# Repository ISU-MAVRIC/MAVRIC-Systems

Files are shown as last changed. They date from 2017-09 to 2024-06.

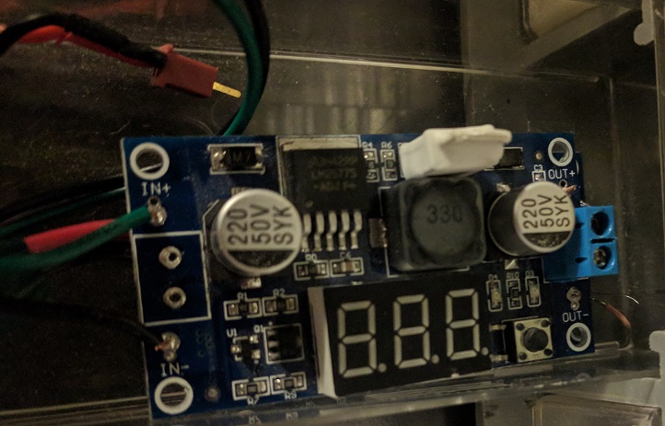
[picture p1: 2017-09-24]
Electrical/Images of Components/Step-Up.jpg

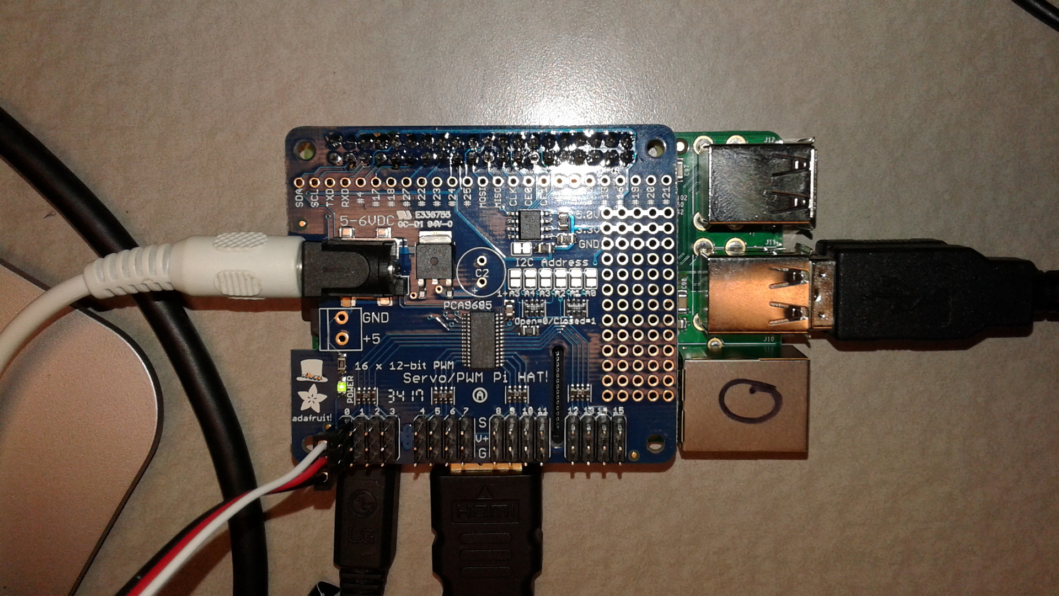
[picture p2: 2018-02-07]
Electrical/Images of Components/Pi-PWM-hat.jpg

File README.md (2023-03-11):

# MAVRIC-Systems
The repository for the Systems Team. Contains all resources pertaining to the Systems Team, including: rover and base station code, custom PCB designs, electrical diagrams, and rover documentation. Clone this repository to your computer with Git Bash, GitHub Desktop, or another Git client to edit files. Talk to the current Systems Team Lead or the current MAVRIC Project Manager to get commit access so you can push your changes to the repository.

## Repository Structure
MAVRIC maintains two rovers as of 12/2020: the previous-generation Phoenix and the next-gen Scarab. The code for Phoenix was captured as a GitHub release and can be viewed by checking out the _Phoenix - Stable_ release, tagged `v1.0.0`. Use `git checkout v1.0.0` in Git Bash or the equivalent feature in your Git client to load the Phoenix code. Each rover's code will be tagged with a release name and version number once it is complete; this repository will otherwise reflect the code state of the most recent rover in development.

Newer code is not backwards-compatible with previous generation rovers. For example, the base station software intended for use with Scarab is not compatible with Phoenix.

## Wiki Documentation
Documentation about MAVRIC rovers, past and present, is recorded using the GitHub Wiki feature. Click the _Wiki_ tab on the MAVRIC-Systems web page to open the wiki, then use the links in the sidebar to navigate to various wiki pages. Most information is up to date and the difference should be very noticeable, but if you are not able to tell the difference between current and outdated information, ask the current Systems Team Lead about it. Remember that this repository contains documentation for multiple rovers, so information that appears outdated may simply document a different rover than the one currently being developed.

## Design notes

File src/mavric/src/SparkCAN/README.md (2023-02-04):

# MAVRIC SparkMax ESC Library

A library for controlling SparkMax Electronic Speed Controllers using python and a CAN Bus.

## IMPORTANT NOTE
*Motor controllers must have ramping enabled if running at more than 50% power, otherwise the motor will try to instantly go to the power level and will stutter.*

## Dependancies

- Python 3 (Not tested on 2.7)
- python-can (https://python-can.readthedocs.io/en/master/)

# Example Control and Encoder Feedback Code

```python
from SparkCAN import SparkBus
import time

#Instantiate SparkBus object
bus = SparkBus(channel="can0", bustype='socketcan', bitrate=1000000)
#Create a new controller with CAN id 1
sparkESC = bus.init_controller(1)
time.sleep(1)
#Set motor to 50% power
sparkESC.percent_output(.5) #50%
#Prints the velocity 10 times, you should be able to see it ramp up as the motor gets up to speed.
for i in range(10):
    print(sparkESC.velocity)
    time.sleep(0.001)
#wait 5 seconds
time.sleep(5)
#Set motor to 0% power
sparkESC.percent_output(0)
```

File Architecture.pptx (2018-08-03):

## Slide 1

Wheel Driver

Wheel Driver

Arm

Legend:
Power
Signal
Module

Power Relays should Have a local override

Arm Control Board

Power Relay

Wheel Driver

Drive Control Board

Master Control Board

Wheel Driver

Power Relay

Power Relay

Communications
(radios)

Master Switch

Battery

Battery

Wheel Driver

Wheel Driver

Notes: Electrical architecture. Shows power systems, components, and communication lines.

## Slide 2

Legend:
Power
Signal
Module

Drive Control Board

Arm

Wheel Driver

Arm Control Board

Wheel Driver

Master Control Board

Wheel Driver

Wheel Driver

Communications
(radios)

Master Switch

Wheel Driver

Battery

Wheel Driver

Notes: Electrical architecture. Shows power systems, components, and communication lines.

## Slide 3

Drive Control Board

Speed Control

Wheel Control

Left

Right

External Debug
(Sees everything, renders whatever we need to the user)
(May comprise of rqt tools)

Soil Science System

Controller
Collection
Sensors

Arm Control Board

- Linear Actuator Driver
- DC Motor Driver

Servo Driver
(smoothing etc.
included)

Right

Left

Commands

ROS Interface

Inverse Kinematics (opt)

ROS Interface

Master Control Board

ROS Interface

ROS Interface

GPS

Base Station Interface

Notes: ROS Architecture. Structure of nodes (lines are topics).

The Comms. Interface nodes will handle communication between the boards. They are intended as the only interface between boards. To be clear: the master control board should not publish or subscribe to internal topics of the other boards.

The base station may communicate over ROS, but that will depend on the network reliability, and on if we are using a TCP/IP enabled communications system.

The Inverse Kinematics node may or may not exist in reality. It will certainty not exist in rev1.

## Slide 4

Motor Driver

Arm Control Board

Master Control Board

Legend:
Power
Signal
Module

5V Reg.

Communications
(network)

Power Source

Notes: Electrical architecture. Shows power systems, components, and communication lines.

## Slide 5

Arm Control Board

Master Control Board

Translation to ROS

Network Port

Analog in

Control System (closed loop)

PWM out

Subscriber

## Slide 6

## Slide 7

/

Drive Board HW/

PCA9685 PWM HAT/
Driver module for the HAT, takes in wither duty cycle or pulse time inputs.
Frequency is set by a parameter (startup)

Arm Board HW/

PCA9685 PWM HAT
Driver module for the HAT, takes in wither duty cycle or pulse time inputs.
Frequency is set by a parameter (startup)

Switch Inputs (PiGPIO)
Reads a GPIO pin and publishes out the results
Frequency is set by a parameter (startup)

Master Board HW/

PCA9685 PWM HAT
Driver module for the HAT, takes in wither duty cycle or pulse time inputs.
Frequency is set by a parameter (startup)

GPS Module (serial)
Retrieves and publishes the current GPS data

Arm/

Actuator Interface
Receives commands for an actuator and publishes them.

Actuator Limiting
Limits the value of an actuator command when configured switches are active.

Mapping
Scales the outputs for the PWM board

Drive/

Drivetrain Interface
Receives commands and publishes them in pairs (left, right)

Drivetrain Hartbeat
Monitors for a gap in the drivetrain command pairs and stops the rover

Drivetrain Control
Subscribes to drive command pairs and outputs the individual motor values

Mapping
Scales the motor outputs for the PWM outputs.

System Cooling/

PID Controller
Monitors temperature and outputs speed to the fans (via PWM controller)

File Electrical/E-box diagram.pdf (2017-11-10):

Room for wires for front two Pis

Main Control | Drive
Science | Arm control

Room for wires for front two Pis

IO port and room for connectors | IO port and room for connectors
H‐Bridge | H‐Bridge

Reserved For Sensors
(Like GPS)

Switch Board of unknown size

Regulator | Regulator
Regulator | Regulator

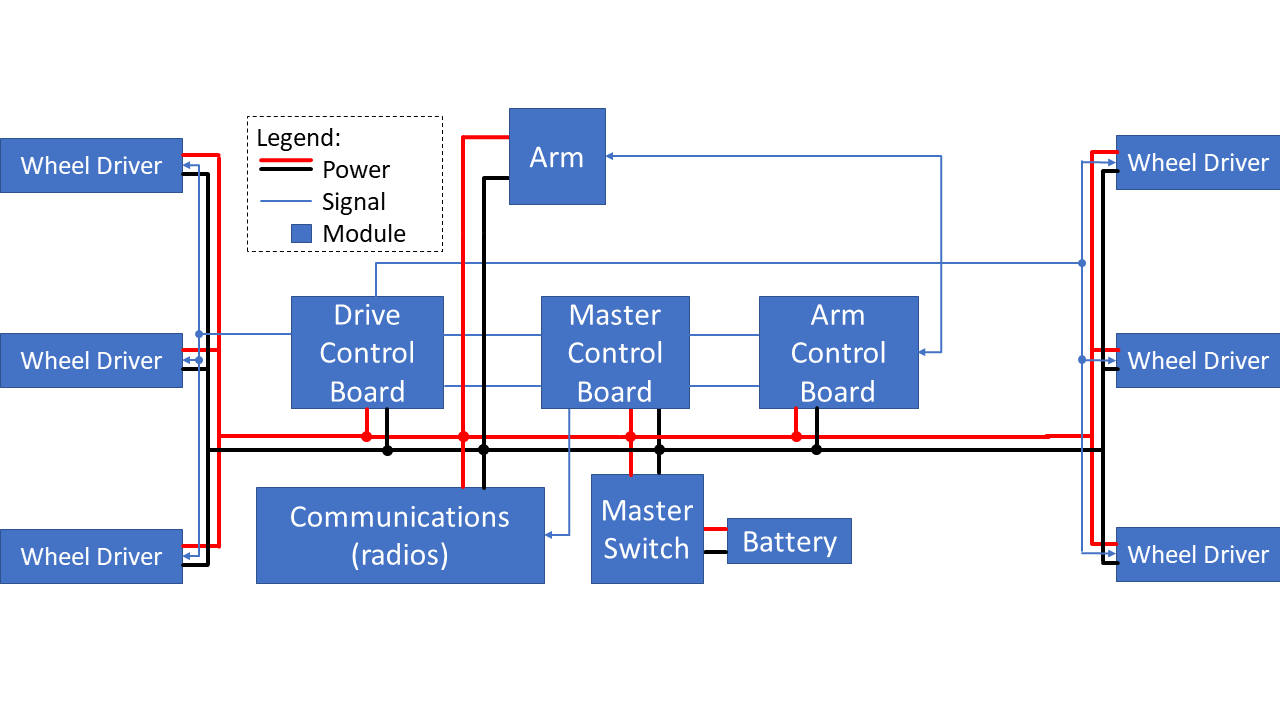
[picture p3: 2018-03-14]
Electrical/ElectricalArchitecture.png

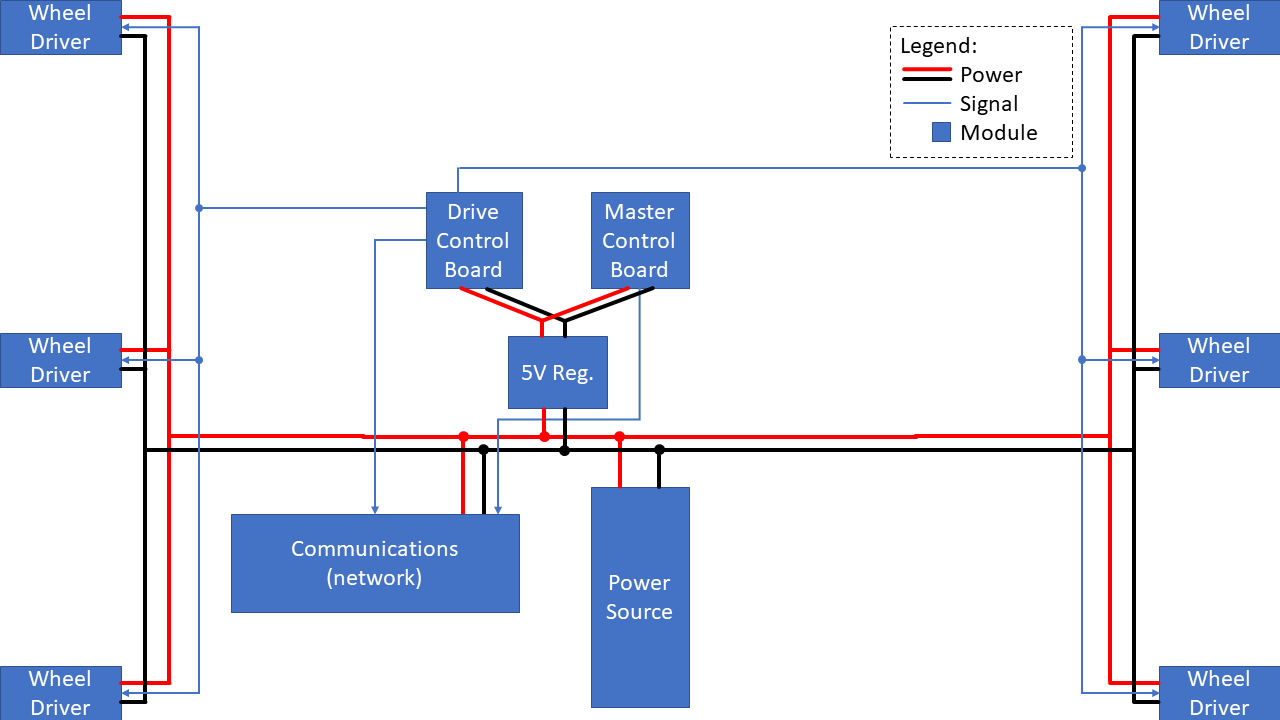
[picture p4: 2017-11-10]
Electrical/Milestone1 Electrical.PNG

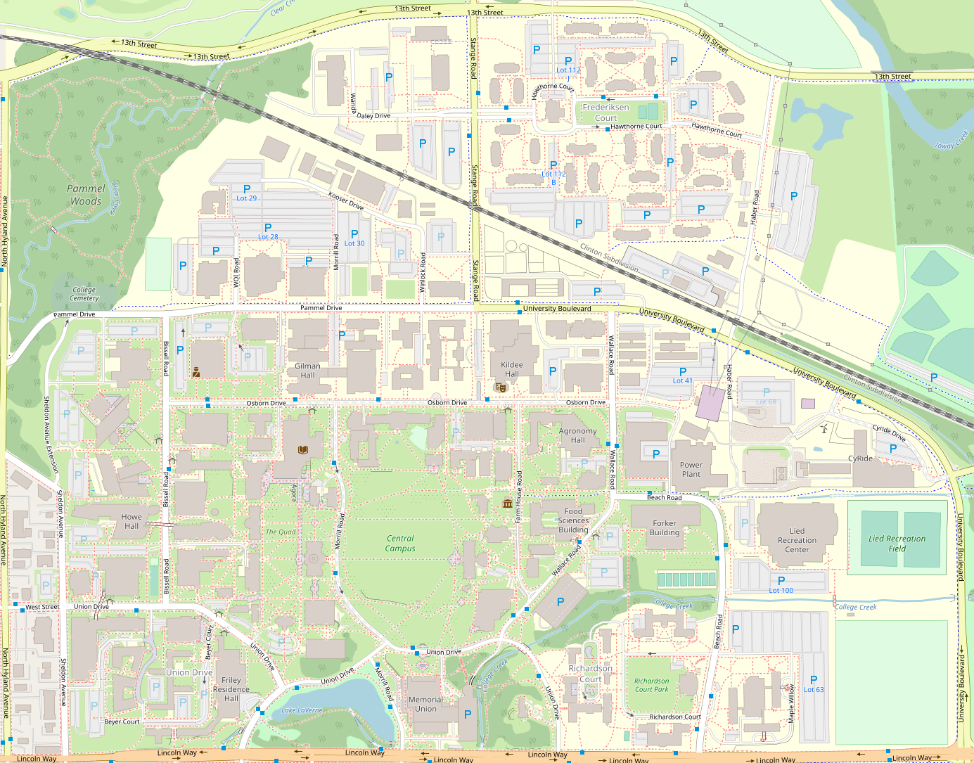
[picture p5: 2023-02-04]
Base Station/Scarab Base Station/maps/map.png

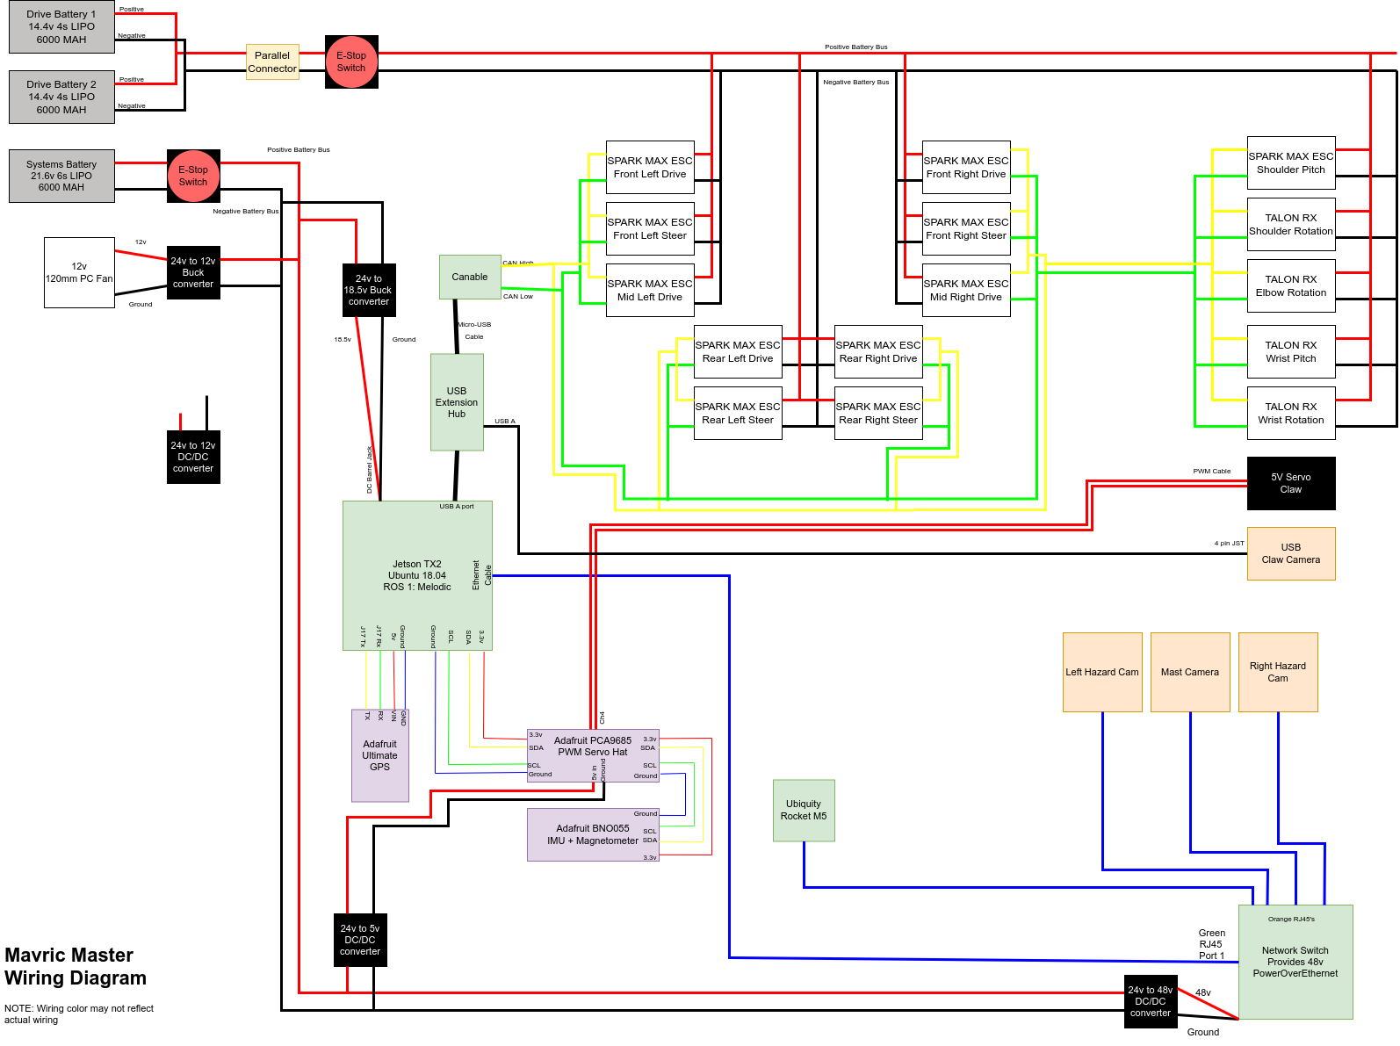
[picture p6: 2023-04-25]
Electrical/MasterDiagram.drawio.png

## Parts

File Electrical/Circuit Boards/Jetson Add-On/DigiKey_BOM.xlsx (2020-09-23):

Qty | Part number | Description | Total
2 | 568-8366-5-ND | PWM Driver IC | $4.52
2 | 296-49939-1-ND | CAN Transceiver IC | $5.36
1 | LTC2309CF#PBF-ND | ADC IC | $7.34
1 | PPPC152LFBN-RC | 30-Pin Header | $1.89
1 | 36-3000-ND | Coin Cell Holder | $0.54
1 | https://www.adafruit.com/product/2223 | GPIO Stacking Header | $2.50
1 | https://www.adafruit.com/product/790 | GPS Module | $29.95
 |  | Grand Total | $19.65

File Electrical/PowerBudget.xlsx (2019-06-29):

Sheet: Component Data
ID | Name | Manufacturer | Source | Notes | Price | Peak Consumption (W) | Constant Consumption (W) | Output (V) | Output Current Limit (A) | Discharge (for batteries) | Battery (mAh) | Thoughput Loss
LiFePo |  |  |  |  |  | 0.0 | 0.0 | 28.8 |  | 10C | 10000.0 | 0.00%
Large LiPo | 22.2 V Lithuim Polymer Battery back | BatterySpace | http://www.batteryspace.com/lipo-battery-pack-tattu-22-2v-12ah-266wh-15c-6s1p.aspx |  | $254.00 | 0.0 | 0.0 | 22.2 |  | 15C | 12000.0 | 0.00%
Small LiPo | 22.2 V Lithuim Polymer Battery back |  |  |  |  | 0.0 | 0.0 | 22.2 |  | 15C | 5200.0 | 0.00%
LiIon | 22.2V Lithium Ion Battery Pack |  |  | Obtained from Lab leftovers | $0.00 |  |  | 21.6 |  | 5C | 7800.0 | 0.00%
Regulator | Adjustable Linear Voltage Regulator | Aihasd | https://www.aliexpress.com/item/DC-Adjustable-Voltage-Regulator-Module-DC-4-5-30V-to-0-8-30V-12A-Buck-Converters/1724570414.html |  | $8.48 | 0.0 | 0.0 |  | 12.0 |  |  | 10.00%
Raspberry Pi | Raspberry Pi 3 Rev 1.2 |  |  |  | $30.00 | 7.0 | 4.0 | 3.3 | 0.5 |  |  | 0.00%
RM5 | Ubiquity Rocket M5 | Ubiquity | http://www.doubleradius.com/s.nl/sc.1/category./.f?search=rocket+m3 |  | $180.00 | 8.0 | 6.0 |  |  |  |  | 0.00%
Victor SP | Victor SP DC Motor Driver | Cross The Road Electronics | https://www.vexrobotics.com/217-9090.html |  | $60.00 | 0.0 | 0.0 | 12.0 | 60.0 |  |  | 10.00%
Talon SRX | Talon SRX DC Motor Driver | Cross The Road Electronics |  |  | $90.00 | 0.0 | 0.0 | [INPUT] | 60.0 |  |  | 10.00%
Wheel Motor | Banebots RS-550 Motor 19300rpm 12V 70.55oz-in | BaneBot | http://robotshop.com/en/banebots-rs-550-motor-12v-19300rpm.html |  | $7.25 | 222.0 | 37.0 |  |  |  |  | 0.00%
20A 24V->12V Regulator | Nextrox DC/DC Converter Regulator 24V Step Down to 12V 20A 240W |  | https://www.amazon.com/Nextrox-Converter-Regulator-Step-Down/dp/B00BWKXTUU | 12-40V input | $16.00 | 0.0 | 0.0 | 12.0 | 20.0 |  |  | 10.00%
Network Switch | 16-Port network switch |  |  |  | $60.00 | 24.0 | 8.0 |  |  |  |  | 0.00%
Power Rail | Virtual Node for system isolation |  |  |  | $0.00 | 0.0 | 0.0 | [INPUT] |  |  |  | 0.00%
PC Fan | ??? |  |  | 12V 4-pin PC Fan | $18.00 | 12.0 | 6.3 |  |  |  |  | 0.00%
IP Camera | ELP 1280720p 1MP Camera |  | https://www.amazon.com/ELP-1280720p-Megapixel-Camera-Network/dp/B00KA4M4WS |  | $20.00 | 12.0 | 6.0 |  |  |  |  | 0.00%
Arm Shoulder |  |  |  |  |  | 200.0 | 24.0 |  |  |  |  | 0.00%
Arm Elbow |  |  |  |  |  | 10.0 | 1.0 |  |  |  |  | 0.00%
Arm Wrist |  |  |  |  |  | 10.0 | 2.0 |  |  |  |  | 0.00%
Jetson TX2 |  |  |  |  |  | 70.0 | 50.0 |  |  |  |  | 0.00%

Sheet: Items
ItemID | Component | Supply Item | Supply Component | Name | Manufacturer | Source | Price | Peak Consumption (W) | Constant Consumption (W) | Output (V) | Output (A) | Battery (mAh) | Thoughput Loss
Primary Battery Pack | Large LiPo |  |  | 22.2 V Lithuim Polymer Battery back | BatterySpace | http://www.batteryspace.com/lipo-battery-pack-tattu-22-2v-12ah-266wh-15c-6s1p.aspx | $254.00 | 0.0 | 0.0 | 22.2 | 180.0 | 12000.0 | 0.00%
E-Box Battery | Small LiPo |  |  | 22.2 V Lithuim Polymer Battery back |  |  |  | 0.0 | 0.0 | 22.2 | 78.0 | 5200.0 | 0.00
Logic Supply | Regulator | E-Box Battery | Small LiPo | Adjustable Linear Voltage Regulator | Aihasd | https://www.aliexpress.com/item/DC-Adjustable-Voltage-Regulator-Module-DC-4-5-30V-to-0-8-30V-12A-Buck-Converters/1724570414.html | $8.48 | 0.0 | 0.0 | 19.5 | 5.1 |  | 10.00%
Network Power | Regulator | E-Box Battery | Small LiPo | Adjustable Linear Voltage Regulator | Aihasd | https://www.aliexpress.com/item/DC-Adjustable-Voltage-Regulator-Module-DC-4-5-30V-to-0-8-30V-12A-Buck-Converters/1724570414.html | $8.48 | 0.0 | 0.0 | 12.0 | 12.0 |  | 10.00%
Transceiver | RM5 | Network Power | Regulator | Ubiquity Rocket M5 | Ubiquity | http://www.doubleradius.com/s.nl/sc.1/category./.f?search=rocket+m3 | $180.00 | 8.0 | 6.0 |  | 0.0 |  | 0.00%
Network Switch | Network Switch | Network Power | Regulator | 16-Port network switch |  |  | $60.00 | 24.0 | 8.0 |  | 0.0 |  | 0.00%
Arm Power | 20A 24V->12V Regulator | Primary Battery Pack | Large LiPo | Nextrox DC/DC Converter Regulator 24V Step Down to 12V 20A 240W |  | https://www.amazon.com/Nextrox-Converter-Regulator-Step-Down/dp/B00BWKXTUU | $16.00 | 0.0 | 0.0 | 12.0 | 20.0 |  | 10.00%
Drivetrain Power | Power Rail | Primary Battery Pack | Large LiPo | Virtual Node for system isolation |  |  | $0.00 | 0.0 | 0.0 | 22.2 | 400.0 |  | 0.00%
FrontRight ESC | Talon SRX | Drivetrain Power | Power Rail | Talon SRX DC Motor Driver | Cross The Road Electronics |  | $90.00 | 0.0 | 0.0 | 22.2 | 60.0 |  | 10.00%
FrontRight Motor | Wheel Motor | FrontRight ESC | Talon SRX | Banebots RS-550 Motor 19300rpm 12V 70.55oz-in | BaneBot | http://robotshop.com/en/banebots-rs-550-motor-12v-19300rpm.html | $7.25 | 222.0 | 37.0 |  | 0.0 |  | 0.00%
MidRight ESC | Talon SRX | Drivetrain Power | Power Rail | Talon SRX DC Motor Driver | Cross The Road Electronics |  | $90.00 | 0.0 | 0.0 | 22.2 | 60.0 |  | 10.00%
MidRight Motor | Wheel Motor | MidRight ESC | Talon SRX | Banebots RS-550 Motor 19300rpm 12V 70.55oz-in | BaneBot | http://robotshop.com/en/banebots-rs-550-motor-12v-19300rpm.html | $7.25 | 222.0 | 37.0 |  | 0.0 |  | 0.00%
BackRight ESC | Talon SRX | Drivetrain Power | Power Rail | Talon SRX DC Motor Driver | Cross The Road Electronics |  | $90.00 | 0.0 | 0.0 | 22.2 | 60.0 |  | 10.00%
BackRight Motor | Wheel Motor | BackRight ESC | Talon SRX | Banebots RS-550 Motor 19300rpm 12V 70.55oz-in | BaneBot | http://robotshop.com/en/banebots-rs-550-motor-12v-19300rpm.html | $7.25 | 222.0 | 37.0 |  | 0.0 |  | 0.00%
FrontLeft ESC | Talon SRX | Drivetrain Power | Power Rail | Talon SRX DC Motor Driver | Cross The Road Electronics |  | $90.00 | 0.0 | 0.0 | 22.2 | 60.0 |  | 10.00%
FrontLeft Motor | Wheel Motor | FrontLeft ESC | Talon SRX | Banebots RS-550 Motor 19300rpm 12V 70.55oz-in | BaneBot | http://robotshop.com/en/banebots-rs-550-motor-12v-19300rpm.html | $7.25 | 222.0 | 37.0 |  | 0.0 |  | 0.00%
MidLeft ESC | Talon SRX | Drivetrain Power | Power Rail | Talon SRX DC Motor Driver | Cross The Road Electronics |  | $90.00 | 0.0 | 0.0 | 22.2 | 60.0 |  | 10.00%
MidLeft Motor | Wheel Motor | MidLeft ESC | Talon SRX | Banebots RS-550 Motor 19300rpm 12V 70.55oz-in | BaneBot | http://robotshop.com/en/banebots-rs-550-motor-12v-19300rpm.html | $7.25 | 222.0 | 37.0 |  | 0.0 |  | 0.00%
BackLeft ESC | Talon SRX | Drivetrain Power | Power Rail | Talon SRX DC Motor Driver | Cross The Road Electronics |  | $90.00 | 0.0 | 0.0 | 22.2 | 60.0 |  | 10.00%
BackLeft Motor | Wheel Motor | BackLeft ESC | Talon SRX | Banebots RS-550 Motor 19300rpm 12V 70.55oz-in | BaneBot | http://robotshop.com/en/banebots-rs-550-motor-12v-19300rpm.html | $7.25 | 222.0 | 37.0 |  | 0.0 |  | 0.00%
Cooling Fans Power | Regulator | E-Box Battery | Small LiPo | Adjustable Linear Voltage Regulator | Aihasd | https://www.aliexpress.com/item/DC-Adjustable-Voltage-Regulator-Module-DC-4-5-30V-to-0-8-30V-12A-Buck-Converters/1724570414.html | $8.48 | 0.0 | 0.0 | 12.0 | 12.0 |  | 0.10
Colling Fan 1 | PC Fan | Cooling Fans Power | Regulator | ??? |  |  | $18.00 | 12.0 | 6.3 |  | 0.0 |  | 0.00
Colling Fan 2 | PC Fan | Cooling Fans Power | Regulator | ??? |  |  | $18.00 | 12.0 | 6.3 |  | 0.0 |  | 0.00
Colling Fan 3 | PC Fan | Cooling Fans Power | Regulator | ??? |  |  | $18.00 | 12.0 | 6.3 |  | 0.0 |  | 0.00
Colling Fan 4 | PC Fan | Cooling Fans Power | Regulator | ??? |  |  | $18.00 | 12.0 | 6.3 |  | 0.0 |  | 0.00
 |  | Cooling Fans Power | Regulator
 |  | Cooling Fans Power | Regulator
 |  | Cooling Fans Power | Regulator
 |  | Cooling Fans Power | Regulator
Hazard Camera 1 | IP Camera | Network Power | Regulator | ELP 1280720p 1MP Camera |  | https://www.amazon.com/ELP-1280720p-Megapixel-Camera-Network/dp/B00KA4M4WS | $20.00 | 12.0 | 6.0 |  | 0.0 |  | 0.00
Hazard Camera 2 | IP Camera | Network Power | Regulator | ELP 1280720p 1MP Camera |  | https://www.amazon.com/ELP-1280720p-Megapixel-Camera-Network/dp/B00KA4M4WS | $20.00 | 12.0 | 6.0 |  | 0.0 |  | 0.00
Hazard Camera 3 | IP Camera | Network Power | Regulator | ELP 1280720p 1MP Camera |  | https://www.amazon.com/ELP-1280720p-Megapixel-Camera-Network/dp/B00KA4M4WS | $20.00 | 12.0 | 6.0 |  | 0.0 |  | 0.00
Arm Shoulder | Arm Shoulder | Arm Power | 20A 24V->12V Regulator |  |  |  |  | 200.0 | 24.0 |  | 0.0 |  | 0.00
Arm Elbow | Arm Elbow | Arm Power | 20A 24V->12V Regulator |  |  |  |  | 10.0 | 1.0 |  | 0.0 |  | 0.00
Arm Wrist1 | Arm Wrist | Arm Power | 20A 24V->12V Regulator |  |  |  |  | 10.0 | 2.0 |  | 0.0 |  | 0.00
Arm Wrist2 | Arm Wrist | Arm Power | 20A 24V->12V Regulator |  |  |  |  | 10.0 | 2.0 |  | 0.0 |  | 0.00
Control Board | Jetson TX2 | Logic Supply | Regulator |  |  |  |  | 70.0 | 50.0 |  | 0.0 |  | 0.00

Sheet: Analysis
ItemID | Supply Item | Input (V) | Output (V) | Peak Output (A) | Constant Output (A) | Peak Input (A) | Constant Input (A) | Thoughput Loss | Self Peak Consumption (W) | Children Peak Consumption (W) | Total Peak Consumption (W) | Self Constant Consumption (W) | Children Constant Consumption (W) | Total Constant Consumption (W)
Primary Battery Pack |  |  | 22.2 | 77.4 | 12.4 |  |  | 0.00 | 0.0 | 1718.2 | 1718.2 | 0.0 | 276.1 | 276.1
E-Box Battery |  |  | 22.2 | 9.2 | 5.3 |  |  | 0.00 | 0.0 | 204.6 | 204.6 | 0.0 | 117.9 | 117.9
Logic Supply | E-Box Battery | 22.2 | 19.5 | 3.6 | 2.6 | 3.5 | 2.5 | 0.10 | 7.0 | 70.0 | 77.0 | 5.0 | 50.0 | 55.0
Network Power | E-Box Battery | 22.2 | 12 | 5.7 | 2.7 | 3.4 | 1.6 | 0.10 | 6.8 | 68.0 | 74.8 | 3.2 | 32.0 | 35.2
Transceiver | Network Power | 12 |  |  |  | 0.7 | 0.5 | 0.00 | 8.0 | 0.0 | 8.0 | 6.0 | 0.0 | 6.0
Network Switch | Network Power | 12 |  |  |  | 2.0 | 0.7 | 0.00 | 24.0 | 0.0 | 24.0 | 8.0 | 0.0 | 8.0
Arm Power | Primary Battery Pack | 22.2 | 12 | 19.2 | 2.4 | 11.4 | 1.4 | 0.10 | 23.0 | 230.0 | 253.0 | 2.9 | 29.0 | 31.9
Drivetrain Power | Primary Battery Pack | 22.2 | 22.2 | 66.0 | 11.0 | 66.0 | 11.0 | 0.00 | 0.0 | 1465.2 | 1465.2 | 0.0 | 244.2 | 244.2
FrontRight ESC | Drivetrain Power | 22.2 | 22.2 | 10.0 | 1.7 | 11.0 | 1.8 | 0.10 | 22.2 | 222.0 | 244.2 | 3.7 | 37.0 | 40.7
FrontRight Motor | FrontRight ESC | 22.2 |  |  |  | 10.0 | 1.7 | 0.00 | 222.0 | 0.0 | 222.0 | 37.0 | 0.0 | 37.0
MidRight ESC | Drivetrain Power | 22.2 | 22.2 | 10.0 | 1.7 | 11.0 | 1.8 | 0.10 | 22.2 | 222.0 | 244.2 | 3.7 | 37.0 | 40.7
MidRight Motor | MidRight ESC | 22.2 |  |  |  | 10.0 | 1.7 | 0.00 | 222.0 | 0.0 | 222.0 | 37.0 | 0.0 | 37.0
BackRight ESC | Drivetrain Power | 22.2 | 22.2 | 10.0 | 1.7 | 11.0 | 1.8 | 0.10 | 22.2 | 222.0 | 244.2 | 3.7 | 37.0 | 40.7
BackRight Motor | BackRight ESC | 22.2 |  |  |  | 10.0 | 1.7 | 0.00 | 222.0 | 0.0 | 222.0 | 37.0 | 0.0 | 37.0
FrontLeft ESC | Drivetrain Power | 22.2 | 22.2 | 10.0 | 1.7 | 11.0 | 1.8 | 0.10 | 22.2 | 222.0 | 244.2 | 3.7 | 37.0 | 40.7
FrontLeft Motor | FrontLeft ESC | 22.2 |  |  |  | 10.0 | 1.7 | 0.00 | 222.0 | 0.0 | 222.0 | 37.0 | 0.0 | 37.0
MidLeft ESC | Drivetrain Power | 22.2 | 22.2 | 10.0 | 1.7 | 11.0 | 1.8 | 0.10 | 22.2 | 222.0 | 244.2 | 3.7 | 37.0 | 40.7
MidLeft Motor | MidLeft ESC | 22.2 |  |  |  | 10.0 | 1.7 | 0.00 | 222.0 | 0.0 | 222.0 | 37.0 | 0.0 | 37.0
BackLeft ESC | Drivetrain Power | 22.2 | 22.2 | 10.0 | 1.7 | 11.0 | 1.8 | 0.10 | 22.2 | 222.0 | 244.2 | 3.7 | 37.0 | 40.7
BackLeft Motor | BackLeft ESC | 22.2 |  |  |  | 10.0 | 1.7 | 0.00 | 222.0 | 0.0 | 222.0 | 37.0 | 0.0 | 37.0
Cooling Fans Power | E-Box Battery | 22.2 | 12 | 4.0 | 2.1 | 2.4 | 1.2 | 0.10 | 4.8 | 48.0 | 52.8 | 2.5 | 25.2 | 27.7
Colling Fan 1 | Cooling Fans Power | 12 |  |  |  | 1.0 | 0.5 | 0.00 | 12.0 | 0.0 | 12.0 | 6.3 | 0.0 | 6.3
Colling Fan 2 | Cooling Fans Power | 12 |  |  |  | 1.0 | 0.5 | 0.00 | 12.0 | 0.0 | 12.0 | 6.3 | 0.0 | 6.3
Colling Fan 3 | Cooling Fans Power | 12 |  |  |  | 1.0 | 0.5 | 0.00 | 12.0 | 0.0 | 12.0 | 6.3 | 0.0 | 6.3
Colling Fan 4 | Cooling Fans Power | 12 |  |  |  | 1.0 | 0.5 | 0.00 | 12.0 | 0.0 | 12.0 | 6.3 | 0.0 | 6.3
Hazard Camera 1 | Network Power | 12 |  |  |  | 1.0 | 0.5 | 0.00 | 12.0 | 0.0 | 12.0 | 6.0 | 0.0 | 6.0
Hazard Camera 2 | Network Power | 12 |  |  |  | 1.0 | 0.5 | 0.00 | 12.0 | 0.0 | 12.0 | 6.0 | 0.0 | 6.0
Hazard Camera 3 | Network Power | 12 |  |  |  | 1.0 | 0.5 | 0.00 | 12.0 | 0.0 | 12.0 | 6.0 | 0.0 | 6.0
Arm Shoulder | Arm Power | 12 |  |  |  | 16.7 | 2.0 | 0.00 | 200.0 | 0.0 | 200.0 | 24.0 | 0.0 | 24.0
Arm Elbow | Arm Power | 12 |  |  |  | 0.8 | 0.1 | 0.00 | 10.0 | 0.0 | 10.0 | 1.0 | 0.0 | 1.0
Arm Wrist1 | Arm Power | 12 |  |  |  | 0.8 | 0.2 | 0.00 | 10.0 | 0.0 | 10.0 | 2.0 | 0.0 | 2.0
Arm Wrist2 | Arm Power | 12 |  |  |  | 0.8 | 0.2 | 0.00 | 10.0 | 0.0 | 10.0 | 2.0 | 0.0 | 2.0
Control Board | Logic Supply | 19.5 |  |  |  | 3.6 | 2.6 | 0.00 | 70.0 | 0.0 | 70.0 | 50.0 | 0.0 | 50.0

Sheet: Results
ItemID | Peak % Capacity | Constant % Capacity | Battery Life (hrs) |  |  | Power Rail | Voltage (V) | Current (A) | Peak Current (A) | Power (W)
 |  |  |  |  |  | Primary Battery Pack | 22.20 | 12.44 | 77.40 | 1718.20
Primary Battery Pack | 43.00% | 6.91% | 0.96 | Status: | GO | E-Box Battery | 22.20 | 5.31 | 9.22 | 204.60
E-Box Battery | 11.82% | 6.81% | 0.98 | Battery Life: | 57.9 min
Logic Supply | 70.00% | 50.00%
Network Power | 47.22% | 22.22%
Transceiver
Network Switch
Arm Power | 95.83% | 12.08%
Drivetrain Power | 16.50% | 2.75%
FrontRight ESC | 16.67% | 2.78%
FrontRight Motor
MidRight ESC | 16.67% | 2.78%
MidRight Motor
BackRight ESC | 16.67% | 2.78%
BackRight Motor
FrontLeft ESC | 16.67% | 2.78%
FrontLeft Motor
MidLeft ESC | 16.67% | 2.78%
MidLeft Motor
BackLeft ESC | 16.67% | 2.78%
BackLeft Motor
Cooling Fans Power | 33.33% | 17.50%
Colling Fan 1
Colling Fan 2
Colling Fan 3
Colling Fan 4
Hazard Camera 1
Hazard Camera 2
Hazard Camera 3
Arm Shoulder
Arm Elbow
Arm Wrist1

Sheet: Motor Characterization
Speed (RPM) | Torque (N·m) | Current (A) | Voltage | K_s | K_t | R | Speed (RPM) | Torque (N·m) | Current (A)
0 | 0.358 | 71.235 | 12 | 0.0008409330918 | 198.98 A/Nm | 0.168 Ohm | 2.38788245e-05 | 0.358 | 71.2350262
142.699 | 0.35442 | 70.56 |  |  |  | Equation | 142.70 | 0.35442 | 70.52267594
285.397 | 0.35084 | 69.885 | Stall Current | Stall Torque | No-Load Speed | Vin=(0.00084093309V/RPM)*RPM +(198.98052011798A/Nm)*(0.16845645492Ohm)*(Load Nm) | 285.40 | 0.35084 | 69.81032568
428.096 | 0.34726 | 69.21 | 71.24 A | 0.36 Nm | 14269.86299 RPM |  | 428.10 | 0.34726 | 69.09797542
570.795 | 0.34368 | 68.535 |  |  |  |  | 570.79 | 0.34368 | 68.38562515
713.493 | 0.3401 | 67.861 |  |  |  |  | 713.49 | 0.3401 | 67.67327489
856.192 | 0.33652 | 67.186 |  |  |  |  | 856.19 | 0.33652 | 66.96092463
998.89 | 0.33294 | 66.511 |  |  |  |  | 998.89 | 0.33294 | 66.24857437
1141.589 | 0.32936 | 65.836 |  |  |  |  | 1141.59 | 0.32936 | 65.53622411
1284.288 | 0.32578 | 65.161 |  |  |  |  | 1284.29 | 0.32578 | 64.82387384
1426.986 | 0.3222 | 64.486 |  |  |  |  | 1426.99 | 0.3222 | 64.11152358
1569.685 | 0.31862 | 63.811 |  |  |  |  | 1569.68 | 0.31862 | 63.39917332
1712.384 | 0.31504 | 63.136 |  |  |  |  | 1712.38 | 0.31504 | 62.68682306
1855.082 | 0.31146 | 62.461 |  |  |  |  | 1855.08 | 0.31146 | 61.9744728
1997.781 | 0.30788 | 61.786 |  |  |  |  | 1997.78 | 0.30788 | 61.26212253
2140.479 | 0.3043 | 61.112 |  |  |  |  | 2140.48 | 0.3043 | 60.54977227
2283.178 | 0.30072 | 60.437 |  |  |  |  | 2283.18 | 0.30072 | 59.83742201
2425.877 | 0.29714 | 59.762 |  |  |  |  | 2425.88 | 0.29714 | 59.12507175
2568.575 | 0.29356 | 59.087 |  |  |  |  | 2568.58 | 0.29356 | 58.41272149
2711.274 | 0.28998 | 58.412 |  |  |  |  | 2711.27 | 0.28998 | 57.70037122
2853.973 | 0.2864 | 57.737 |  |  |  |  | 2853.97 | 0.2864 | 56.98802096
2996.671 | 0.28282 | 57.062 |  |  |  |  | 2996.67 | 0.28282 | 56.2756707
3139.37 | 0.27924 | 56.387 |  |  |  |  | 3139.37 | 0.27924 | 55.56332044
3282.068 | 0.27566 | 55.712 |  |  |  |  | 3282.07 | 0.27566 | 54.85097018
3424.767 | 0.27208 | 55.037 |  |  |  |  | 3424.77 | 0.27208 | 54.13861991
3567.466 | 0.2685 | 54.363 |  |  |  |  | 3567.47 | 0.2685 | 53.42626965
3710.164 | 0.26492 | 53.688 |  |  |  |  | 3710.16 | 0.26492 | 52.71391939
3852.863 | 0.26134 | 53.013 |  |  |  |  | 3852.86 | 0.26134 | 52.00156913
3995.562 | 0.25776 | 52.338 |  |  |  |  | 3995.56 | 0.25776 | 51.28921887
4138.26 | 0.25418 | 51.663 |  |  |  |  | 4138.26 | 0.25418 | 50.5768686
4280.959 | 0.2506 | 50.988 |  |  |  |  | 4280.96 | 0.2506 | 49.86451834
4423.658 | 0.24702 | 50.313 |  |  |  |  | 4423.66 | 0.24702 | 49.15216808
4566.356 | 0.24344 | 49.638 |  |  |  |  | 4566.36 | 0.24344 | 48.43981782
4709.055 | 0.23986 | 48.963 |  |  |  |  | 4709.05 | 0.23986 | 47.72746756
4851.753 | 0.23628 | 48.288 |  |  |  |  | 4851.75 | 0.23628 | 47.01511729
4994.452 | 0.2327 | 47.614 |  |  |  |  | 4994.45 | 0.2327 | 46.30276703
5137.151 | 0.22912 | 46.939 |  |  |  |  | 5137.15 | 0.22912 | 45.59041677
5279.849 | 0.22554 | 46.264 |  |  |  |  | 5279.85 | 0.22554 | 44.87806651
5422.548 | 0.22196 | 45.589 |  |  |  |  | 5422.55 | 0.22196 | 44.16571625
5565.247 | 0.21838 | 44.914 |  |  |  |  | 5565.25 | 0.21838 | 43.45336598
5707.945 | 0.2148 | 44.239 |  |  |  |  | 5707.95 | 0.2148 | 42.74101572
5850.644 | 0.21122 | 43.564 |  |  |  |  | 5850.64 | 0.21122 | 42.02866546
5993.342 | 0.20764 | 42.889 |  |  |  |  | 5993.34 | 0.20764 | 41.3163152
6136.041 | 0.20406 | 42.214 |  |  |  |  | 6136.04 | 0.20406 | 40.60396494
6278.74 | 0.20048 | 41.539 |  |  |  |  | 6278.74 | 0.20048 | 39.89161467
6421.438 | 0.1969 | 40.865 |  |  |  |  | 6421.44 | 0.1969 | 39.17926441
6564.137 | 0.19332 | 40.19 |  |  |  |  | 6564.14 | 0.19332 | 38.46691415
6706.836 | 0.18974 | 39.515 |  |  |  |  | 6706.84 | 0.18974 | 37.75456389
6849.534 | 0.18616 | 38.84 |  |  |  |  | 6849.53 | 0.18616 | 37.04221363
6992.233 | 0.18258 | 38.165 |  |  |  |  | 6992.23 | 0.18258 | 36.32986336
7134.932 | 0.179 | 37.49 |  |  |  |  | 7134.93 | 0.179 | 35.6175131
7277.63 | 0.17542 | 36.815 |  |  |  |  | 7277.63 | 0.17542 | 34.90516284
7420.329 | 0.17184 | 36.14 |  |  |  |  | 7420.33 | 0.17184 | 34.19281258
7563.027 | 0.16826 | 35.465 |  |  |  |  | 7563.03 | 0.16826 | 33.48046232
7705.726 | 0.16468 | 34.79 |  |  |  |  | 7705.73 | 0.16468 | 32.76811205
7848.425 | 0.1611 | 34.116 |  |  |  |  | 7848.42 | 0.1611 | 32.05576179
7991.123 | 0.15752 | 33.441 |  |  |  |  | 7991.12 | 0.15752 | 31.34341153
8133.822 | 0.15394 | 32.766 |  |  |  |  | 8133.82 | 0.15394 | 30.63106127
8276.521 | 0.15036 | 32.091 |  |  |  |  | 8276.52 | 0.15036 | 29.918711
8419.219 | 0.14678 | 31.416 |  |  |  |  | 8419.22 | 0.14678 | 29.20636074
8561.918 | 0.1432 | 30.741 |  |  |  |  | 8561.92 | 0.1432 | 28.49401048
8704.616 | 0.13962 | 30.066 |  |  |  |  | 8704.62 | 0.13962 | 27.78166022
8847.315 | 0.13604 | 29.391 |  |  |  |  | 8847.32 | 0.13604 | 27.06930996
8990.014 | 0.13246 | 28.716 |  |  |  |  | 8990.01 | 0.13246 | 26.35695969
9132.712 | 0.12888 | 28.041 |  |  |  |  | 9132.71 | 0.12888 | 25.64460943
9275.411 | 0.1253 | 27.367 |  |  |  |  | 9275.41 | 0.1253 | 24.93225917
9418.11 | 0.12172 | 26.692 |  |  |  |  | 9418.11 | 0.12172 | 24.21990891
9560.808 | 0.11814 | 26.017 |  |  |  |  | 9560.81 | 0.11814 | 23.50755865
9703.507 | 0.11456 | 25.342 |  |  |  |  | 9703.51 | 0.11456 | 22.79520838
9846.205 | 0.11098 | 24.667 |  |  |  |  | 9846.21 | 0.11098 | 22.08285812
9988.904 | 0.1074 | 23.992 |  |  |  |  | 9988.90 | 0.1074 | 21.37050786
10131.603 | 0.10382 | 23.317 |  |  |  |  | 10131.60 | 0.10382 | 20.6581576
10274.301 | 0.10024 | 22.642 |  |  |  |  | 10274.30 | 0.10024 | 19.94580734
10417 | 0.09666 | 21.967 |  |  |  |  | 10417.00 | 0.09666 | 19.23345707
10559.699 | 0.09308 | 21.292 |  |  |  |  | 10559.70 | 0.09308 | 18.52110681
10702.397 | 0.0895 | 20.618 |  |  |  |  | 10702.40 | 0.0895 | 17.80875655
10845.096 | 0.08592 | 19.943 |  |  |  |  | 10845.10 | 0.08592 | 17.09640629
10987.795 | 0.08234 | 19.268 |  |  |  |  | 10987.79 | 0.08234 | 16.38405603
11130.493 | 0.07876 | 18.593 |  |  |  |  | 11130.49 | 0.07876 | 15.67170576
11273.192 | 0.07518 | 17.918 |  |  |  |  | 11273.19 | 0.07518 | 14.9593555
11415.89 | 0.0716 | 17.243 |  |  |  |  | 11415.89 | 0.0716 | 14.24700524
11558.589 | 0.06802 | 16.568 |  |  |  |  | 11558.59 | 0.06802 | 13.53465498
11701.288 | 0.06444 | 15.893 |  |  |  |  | 11701.29 | 0.06444 | 12.82230472
11843.986 | 0.06086 | 15.218 |  |  |  |  | 11843.99 | 0.06086 | 12.10995445
11986.685 | 0.05728 | 14.543 |  |  |  |  | 11986.68 | 0.05728 | 11.39760419
12129.384 | 0.0537 | 13.869 |  |  |  |  | 12129.38 | 0.0537 | 10.68525393
12272.082 | 0.05012 | 13.194 |  |  |  |  | 12272.08 | 0.05012 | 9.972903668
12414.781 | 0.04654 | 12.519 |  |  |  |  | 12414.78 | 0.04654 | 9.260553406
12557.479 | 0.04296 | 11.844 |  |  |  |  | 12557.48 | 0.04296 | 8.548203144
12700.178 | 0.03938 | 11.169 |  |  |  |  | 12700.18 | 0.03938 | 7.835852882
12842.877 | 0.0358 | 10.494 |  |  |  |  | 12842.88 | 0.0358 | 7.12350262
12985.575 | 0.03222 | 9.819 |  |  |  |  | 12985.58 | 0.03222 | 6.411152358
13128.274 | 0.02864 | 9.144 |  |  |  |  | 13128.27 | 0.02864 | 5.698802096
13270.973 | 0.02506 | 8.469 |  |  |  |  | 13270.97 | 0.02506 | 4.986451834
13413.671 | 0.02148 | 7.794 |  |  |  |  | 13413.67 | 0.02148 | 4.274101572
13556.37 | 0.0179 | 7.12 |  |  |  |  | 13556.37 | 0.0179 | 3.56175131
13699.068 | 0.01432 | 6.445 |  |  |  |  | 13699.07 | 0.01432 | 2.849401048
13841.767 | 0.01074 | 5.77 |  |  |  |  | 13841.77 | 0.01074 | 2.137050786
13984.466 | 0.00716 | 5.095 |  |  |  |  | 13984.47 | 0.00716 | 1.424700524
14127.164 | 0.00358 | 4.42 |  |  |  |  | 14127.16 | 0.00358 | 0.712350262
14269.863 | 0 | 3.745 |  |  |  |  | 14269.86 | 0 | 0

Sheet: Costs
Item | Component Name | Cost | Component | Quantity | Total Cost
 |  |  | Banebots RS-550 Motor 19300rpm 12V 70.55oz-in | 6 | $43.50
Primary Battery Pack | 22.2 V Lithuim Polymer Battery back | $254.00 | Raspberry Pi 3 Rev 1.2 | 1 | $30.00
E-Box Battery | 22.2 V Lithuim Polymer Battery back |  | Adjustable Linear Voltage Regulator | 2 | $16.96
Logic Supply | Adjustable Linear Voltage Regulator | $8.48 | Ubiquity Rocket M5 | 1 | $180.00
Network Power | Adjustable Linear Voltage Regulator | $8.48 | Nextrox DC/DC Converter Regulator 24V Step Down to 12V 20A 240W | 2 | $32.00
Transceiver | Ubiquity Rocket M5 | $180.00 | Virtual Node for system isolation | 2 | $0.00
Network Switch | 16-Port network switch | $60.00 | Talon SRX DC Motor Driver | 6 | $540.00
Arm Power | Nextrox DC/DC Converter Regulator 24V Step Down to 12V 20A 240W | $16.00 | 22.2 V Lithuim Polymer Battery back | 1 | $254.00
Drivetrain Power | Virtual Node for system isolation | $0.00 | 22.2V Lithium Ion Battery Pack | 1 | $0.00
FrontRight ESC | Talon SRX DC Motor Driver | $90.00 | ??? | 8 | $144.00
FrontRight Motor | Banebots RS-550 Motor 19300rpm 12V 70.55oz-in | $7.25 | ELP 1280720p 1MP Camera | 3 | $60.00
MidRight ESC | Talon SRX DC Motor Driver | $90.00 | 16-Port network switch | 1 | $60.00
MidRight Motor | Banebots RS-550 Motor 19300rpm 12V 70.55oz-in | $7.25 | Grand Total | 34 | $1360.46
BackRight ESC | Talon SRX DC Motor Driver | $90.00
BackRight Motor | Banebots RS-550 Motor 19300rpm 12V 70.55oz-in | $7.25
FrontLeft ESC | Talon SRX DC Motor Driver | $90.00
FrontLeft Motor | Banebots RS-550 Motor 19300rpm 12V 70.55oz-in | $7.25
MidLeft ESC | Talon SRX DC Motor Driver | $90.00
MidLeft Motor | Banebots RS-550 Motor 19300rpm 12V 70.55oz-in | $7.25
BackLeft ESC | Talon SRX DC Motor Driver | $90.00
BackLeft Motor | Banebots RS-550 Motor 19300rpm 12V 70.55oz-in | $7.25
Cooling Fans Power | Adjustable Linear Voltage Regulator | $8.48
Colling Fan 1 | ??? | $18.00
Colling Fan 2 | ??? | $18.00
Colling Fan 3 | ??? | $18.00
Colling Fan 4 | ??? | $18.00
Hazard Camera 1 | ELP 1280720p 1MP Camera | $20.00
Hazard Camera 2 | ELP 1280720p 1MP Camera | $20.00
Hazard Camera 3 | ELP 1280720p 1MP Camera | $20.00
Arm Shoulder
Arm Elbow
Arm Wrist1
Arm Wrist2
Control Board
Total |  | 1250.94

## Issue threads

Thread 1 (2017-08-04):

Arm - Develop Hardware Drivers

Talonj123, 2017-08-04:
Develop circuits to drive the Arm actuators, our actuators are all DC motors, so we need PWM signals to drive them, more than the Raspberry Pi can provide.

Talonj123, 2018-08-04:
We have a driver for the PCA9685 HAT, it currently only supports one PCA9685 chip per Pi, but we can fairly easily add an address parameter and allow the launch file to give the address of a particular chip. This will probably only matter if we roll our own boards with multiple chips for multiple PWM frequencies (the PCA9685 has 16 outputs, I can't imagine we will need more than that on a single Pi).

Talonj123, 2018-08-04:
We also have a Pi GPIO input driver. That lets us interface switches and other single-wire digital inputs.

Talonj123, 2018-08-04:
We may still need:
 - an ADC of some sort for feedback (enhancement)
 - a Pi GPIO output for controlling relays and other digital outputs

Talonj123, 2018-08-09:
I'm going to count this as done, we can open a new issue later if we need more hardware.

Closed 2018-08-09.

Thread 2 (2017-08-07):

Arm - Develop Firmware Drivers

Talonj123, 2017-08-07:
We need firmware drivers to run the hardware. ATM, it looks like all out motors are DC motors, so we will use PWM control (Victor SP ESCs)

Talonj123, 2018-08-04:
see #1

Closed 2018-08-04.

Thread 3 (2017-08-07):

Power budget design

Talonj123, 2017-08-07:
@matgyver can you take a look at the power budget spreadsheet?
https://github.com/m2i/MAVRIC-Electrical/blob/master/Electrical/PowerBudget.xlsm

I did everything in terms of power instead of current to allow for regulators and such. I know that for switches, the voltage is irrelevant, but the math can be done at the voltage of the switched line. It seemed like a simple way to make it all work.

Talonj123, 2017-08-07:
If you have a preferred template, I'd love to use it.

matgyver, 2017-08-07:
I would keep track of both voltage and current as well.  In a large system
like this, you will have multiple regulators and different voltages.  You
will want to track the current draw on each rail.  I've added you to a
HABET one we did a few years ago.

On Mon, Aug 7, 2017 at 11:27 AM, James Talbert <notifications@github.com>
wrote:

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

--
Matthew E. Nelson, M.S.
KB0MGQ
Personal website
www.rfgeeks.com

President/Co-Founder Aerodyne Labs
www.aerodynelabs.com

President/Co-Founder Stratospheric Ballooning Association
www.stratoballooning.org

Talonj123, 2017-08-07:
Is that here on GitHub?

matgyver, 2017-08-07:
Google Spreadsheet, check your gmail.

Talonj123, 2017-08-08:
I've updated it to call out current and voltage (see the Elaboration tab). I'll post a detailed guide on the wiki

Closed 2017-08-08.

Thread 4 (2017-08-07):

External Communication Interface

Talonj123, 2017-08-07:
We must choose an interface between the rover and base station. There are a few options:

| Transceiver                                                                         | Frequency | Protocol            | Cost    |
|---------------------------------------------------------------|-------------|------------------|---------|
| [RFD 900](https://www.google.com/search?q=RFD900)   | 900 MHz   | Serial UART       | ~$100 |
| [Rocket M900](https://www.ubnt.com/airmax/rocketm/) | 900 MHz   | Network Bridge | ~$180 |
| [Rocket M2](https://www.ubnt.com/airmax/rocketm/)     | 2.4 GHz     | Network Bridge | ~$80   |
| [Rocket M3](https://www.ubnt.com/airmax/rocketm/)     | 3 GHz        | Network Bridge | ~$180   |
| [Rocket M365](https://www.ubnt.com/airmax/rocketm/) | 3.65 GHz   | Network Bridge | ~$180 |
| [Rocket M5](https://www.ubnt.com/airmax/rocketm/)     | 5 GHz        | Network Bridge | ~$80 |
| [HK Pilot](https://hobbyking.com/en_us/hkpilot-transceiver-telemetry-radio-set-v2-915mhz.html) | 915 MHz        | Serial UART | ~$35 |

The preferred choice (budget permitting) is the Rocket M3.

Talonj123, 2017-09-24:
Depends on #5.

Talonj123, 2017-10-01:
We have budgeted $600 to purchase Rocket M3 endpoints. Until we obtain these, we should be able to work with the M5 antennas and transceivers we have. The communication structure should remain the same, as both act as a network bridge.

Closed 2017-10-01.

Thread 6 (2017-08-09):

Drive System - Power Regulation

Talonj123, 2017-08-09:
Our current power needs for the DC motor bus peak at just shy of 550 Amps at 12 V, that's 6.6 kW. My searches have not revealed any regulators that fit a viable form factor and also provide that much juice. With our regulators from last year, we would need 46 of them in parallel to get this much throughput.

Does anyone have thoughts on getting that much juice or how to reduce the requirement?
I don't know how to get a nominal load for the motors, can I just take some percentage of the stall load? If so, what percentage?

Talonj123, 2017-08-09:
@matgyver, Any words of wisdom?

Talonj123, 2017-08-09:
Would 24V motors be better?

matgyver, 2017-08-09:
Yes, the higher the voltage the lower your current goes (P=VI).  6.6 kw seems high, what is the torque requirements for the motors?  Is that peak or continuous?

Talonj123, 2017-08-09:
The 6.6 kW comes from stall. I know that's not normal operating conditions, but I don't want the rover to burn out if something goes wrong.

|              | Stall        | Rated        |
|----------|-----------|------------|
| Torque  | 70 oz-in | 7.86 oz-in |
| Current | 85 A        | ? [not given] |

Talonj123, 2017-08-09:
We don't currently have a defined requirement for how much torque we need out of the motors. For the most part, our issue has been ground slippage, not motor power, though I didn't see it on the hills at competition, where the ground might be harder.

Talonj123, 2017-10-01:
More information on motors/power:
It looks like the voltage will define the speed the motor goes at (might be for brushed DC only) while the current is consumed proportional to output power (torque*speed). Using an ESC with brushless DC motors might give us good control of speed, but it will likely try to accelerate quickly (max torque). As such, we might want to ramp the speed so that the acceleration is limited, that way we don't use too much current.

@jraymer1 Can you confirm/reject any of this? I haven't done the research directly, just put some things together from other people.

Talonj123, 2018-01-17:
We have decided to operate the drive motors directly off the battery, so this is a non-issue.

Closed 2018-01-17.

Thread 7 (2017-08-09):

Quadrature Decoders

Talonj123, 2017-08-09:
Some of our motors have quadrature encoders (on the arm) built in. To facilitate easier use, I am looking at decoder chips that can offload the timing requirements to a dedicated circuit. Here's what I've found

 * http://www.semiconductorstore.com/cart/pc/viewPrd.asp?idproduct=47635
 * https://www.usdigital.com/products/interfaces/ics/LFLS7366R-S
 * https://www.usdigital.com/products/interfaces/ics/LFLS7166R-S

| Option          | # Encoders | Price  | Interface |
|---------------|--------------|-------|-----------|
| iC-MD           | 3                 | ~$20 | SPI          |
| LFLS7366R-S | 1                 | ~$5   | SPI          |
| ~~LFLS7166R-S~~ | ~~1~~                 | ~~~$12~~ | ~~Three-state bus~~ |

Part of task #1.

The 12 RPM motor needs at least 16 bits for a full revolution.
The 26 RPM motor needs at least 13 bits for a full revolution.

Talonj123, 2017-08-10:
Looks like we have potentiometers planned in the joints. The encoders are not required for control, but are still a way to improve performance (year 2?). Using the encoders would reduce signal noise, and bring the useful precision up to at least 13 bits with these motors.

**Some form of absolute measurement would still be needed, preferably a potentiometer, so that the arm could initialize without movement.**

Closed 2017-08-10.

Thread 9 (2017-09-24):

PID Control Design (Wheels)

Talonj123, 2017-09-24:
- [ ] Motor specs from Mechanical
 - [ ] Motor testing for transfer function
 - [ ] Laplace-domain Modeling
 - [ ] Discreet modeling

 - [ ] Motor feedback circuitry

Talonj123, 2017-10-01:
It looks like BLDC motor controllers have speed control built in (as I understand it, they have to know the speed to control the coils) so the transfer function of the motor may not be as important. We still want some ramping, and PID may give better response times.

Closed 2018-01-17.

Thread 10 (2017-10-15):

Motors/Batteries/Power Supplies

Talonj123, 2017-10-15:
My current understanding:

We do not know how to calculate the power requirements for out motors. As such, we don't know how to pick power supplies for the motors (ones that can supply stall current are prohibitively expensive and large). Additionally, to use the batteries directly, we need to get 3S batteries, which are apparently hard to get (without buying from China, which I'm told M:2:I doesn't like to do).

Can anyone shed light on any of these problems?

Talonj123, 2017-10-15:
One suggestion was to use diodes to get the voltage drop from the batteries to the motors. I feel that is a bad idea due to the currents involved.

Closed 2018-01-17.

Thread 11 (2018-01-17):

Drive System Assembly

Talonj123, 2018-01-17:
- [x] E-Box Wiring
 - [x] Motor Wiring

Talonj123, 2018-08-04:
The drive system functions correctly (hardware-wise). There were some problems with the power system, but that got solved by separating the logic and motor power systems.

Closed 2018-08-04.

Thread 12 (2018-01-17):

Drive System Testing

Talonj123, 2018-01-17:
Report the status here as we test:
Current Status: The DTS node is able to control Victor SP ESCs with a ~3 ms period PWM.

We have the logic boards (Pi's + HATs) running on a separate battery which has eliminated the problems caused by the inductive load of the motors on the main battery.

We have achieved reliable driving in the atrium for about 10 minutes (ended by safe, planned shutdown, not failure).

We have several hours of drive time on the system without failure, and even more powerful, it has worked on startup reliably.

Talonj123, 2018-08-11:
We have been able to test outdoors at range. The rover moved faster than people wanted to walk :) and was controllable (without buildings in the way) up to 300 meters on grass/sidewalks.

Talonj123, 2018-10-03:
Later drive testing worked up to 0.2 mi. The drive system software and wiring has been reliable.

Closed 2018-12-06.

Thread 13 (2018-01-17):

Drive Wheel Control Ramping

Talonj123, 2018-01-17:
Eventually (this is optional for 2018) we want to put ramping controls on the wheels so that we do not have sudden jumps in current, resulting in arcing. We can discuss details (rates, deadbands, etc.) below.

Talonj123, 2018-08-04:
This is done. There are different rates for ramping towards 0 and away from 0. The idea is that we should be able to stop very quickly.

Closed 2018-08-04.

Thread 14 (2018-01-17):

Compass and GPS Sensors

Talonj123, 2018-01-17:
We want to have compass and GPS sensors for the operator to keep track of rover position. I think we have some in the cabinet, but I'm not sure. The task here is to find out if we have it, post model numbers (or any other identifying information) and look for documentation.

Talonj123, 2018-07-21:
Turns out this is just a function of the GPS module when in motion

Talonj123, 2018-07-27:
GPS module integrated into rover.

Closed 2018-07-27.

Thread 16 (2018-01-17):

GPS interface to Raspberry Pi

Talonj123, 2018-01-17:
The GPS module needs to be accessible to the Raspberry Pi. There should be ROS/python libraries or sample code to interpret NMEA strings (the GPS output) We need to publish latitude and longitude to ROS topics periodically.

Talonj123, 2018-07-27:
Done

Closed 2018-07-27.

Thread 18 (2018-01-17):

Data Interface to new ESCs (Talon SRX)

ghost, 2018-01-17:
The [Talon SRX](https://www.vexrobotics.com/217-8080.html) units have 2 interface options. We can get access to internal PID control by using CAN bus.

Talonj123, 2018-08-09:
I don't know if the PID only uses an external sensor, or if it can use something with the motor current draw. I'm not envisioning this really mattering for us. The only case I can think of where it would is if we needed to know the speed of each wheel for diagnostics.

Closed 2023-02-04.

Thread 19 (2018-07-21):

Drive System Power Draw Profiling

Talonj123, 2018-07-21:
Use this thread to put any information about the power draw of the drive system.

On the cart, the primary battery (draw from motors) is about 10A for a brief period during a direction switch (+40% ESC output to -40% ESC output) using the EXTECH meter the lab has.

On the ground I think it was 15A (hard to tell with the rover moving) which comes out to 330W. This is well within the budgeted 600W for all 6 wheels.

Talonj123, 2018-07-28:
We were ale to measure peaks near 30A when going from stopped to moving at 40% ESC output and 60A when reversing (-40% to 40%). The cruising current was 5A Those numbers are total for all 6 wheels. This is better than anticipated. The updated power budget sheet has 2 hrs of drive time.

Talonj123, 2018-07-28:
@GageLochner we how have an estimated 2 hrs of driving, and 3 hrs of the E-Box

Closed 2018-08-04.

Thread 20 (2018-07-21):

E-Box Wiring

Talonj123, 2018-07-21:
We should have some space between the black plate and the bottom of the box to run wires. We want to be able to remove the plate from the E-Box fairly easily, so we may need to cut down the plate a bit to fit past the bus bars.

Additionally, any long wires need to be labeled with what they connect to or what signal/voltage they carry. For XT-90 connectors, we can put a small label on the face of the connector, but XT60 cables will need a flag-style label. Color coding is insufficient (it has historically been far too easy to run out of the correct size+color of wire).

Talonj123, 2018-07-26:
Done (for now). Things can always be improved. After looking at the airflow, I think it would be best to flip the Pi's 90°, that way the GPIO header is in line with the air flow and blocks it less. See the model here: https://cad.onshape.com/documents/4067eebdb84b1e7dcf48b6ed/w/7275f620d179fd8318a6fadf/e/2da58f6f15de00c0581ae15d

Talonj123, 2018-08-09:
I have implemented the model above. We are missing a couple cables (4" flat Ethernet) and a couple Pi's still, but it's coming along nicely.

Closed 2018-08-09.

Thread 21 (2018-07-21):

Suspension Wiring

Talonj123, 2018-07-21:
The suspension wires are currently too long. We need to sit down with someone from mechanical and look at options for running the wires into the chassis easier (they barely fit through the hole right now). If there isn't another option, we still need to redo the bullet connectors, putting them at the right length on the wires.

Talonj123, 2018-08-11:
that hole might be getting smaller, the solution from mechanical is to do the wiring with the suspension detached.

Closed 2018-12-06.

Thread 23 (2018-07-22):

Weight reduction

ghost, 2018-07-22:
As the Rover needs to be light, we should think of ways to reduce electronics weight.

# 'Free' items
These are items that do not negatively impact performance.
 - [ ] Clean up suspension wiring (reduce excess length
   - Savings unknown

# Trade-off items
These items may reduce performance/capacity but also reduce weight. More analysis is needed before deciding to do them (add sub-bullets with information)
 - [ ] Replace 5V regulators with 3A BEC units.
   - Each Pi consumes up to ~500mA (full load)
   - 3A units seem to be smaller than the ones we use, and should safely power 4 Pi's (needs testing)
 - [ ] Reduce wire size
   - Evaluate the sizes and loads of each of our wires (particularly our 8-AWG wires). We want to keep enough capacity to handle the max current, but we rarely if ever use the maximum possible current.

# Unclassified
Put ideas that may or may not impact performance here.

Talonj123, 2018-08-01:
We can safely go as small as 22 AWG for the arm actuator, which would be the lightest option. We should probably also put all those wires in one locking connector.

http://www.powerstream.com/Wire_Size.htm

Closed 2023-02-04.

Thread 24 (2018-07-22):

Arm motors current draw

Talonj123, 2018-07-22:
For worm drives, we will need to work with the mechanical team (friction depends on speed apparently).

We need to start with the torque each motor will be subjected to (before gearbox/worm drive) and them find the speed/current from the motor curves for that load. The load calculation should include the arm (worst case is fully extended) the claw, and the 5kg load in the claw.

At the time of this writing, we have regulators to give a total of 40A at 12V. This in in 2 20A modules, so hopefully we can split the motors into that cleanly.

Talonj123, 2018-08-09:
Experimentally, the motors all pull 0.5-1.5A under load, so we can realistically fit them on the one regulator.

Talonj123, 2018-08-09:
Experimentally, the motors all pull 0.5-1.5A under load, so we can realistically fit them on the one regulator.

Closed 2018-08-11.

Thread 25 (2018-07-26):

GPS HAT requires a button to be pressed on startup

Talonj123, 2018-07-26:
It is easy to forget to do this, especially, if we have a restart/e-stop hit in the field at competition. Find a way to not need the powerkey to be shorted on startup.

Talonj123, 2018-07-26:
Nevermind, I just soldered across the button. It looks like it can be pressed indefinitely.

Closed 2018-07-26.

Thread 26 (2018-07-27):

Battery Voltage Monitor

ghost, 2018-07-27:
We need to measure the voltage of the batteries.

Talonj123, 2018-07-27:
The [pimoroni Automation pHAT](https://www.adafruit.com/product/3289) has a 24V ADC, which would work for anything less than 6S. We are using a 6S battery for the drive system, so we will need a voltage divider anyways.

We might be able to get away with using the 24V ADC as long as we are okay with not knowing the difference between 90% charged and 100% charged. THe battery is usually around 23V, and is only above 24V for a short time. We could do a resistor and a diode string or something if the board is not internally tolerant of 25.2V (6S LiPo pack maximum)

Talonj123, 2018-08-11:
Will Rickert is designing a board for us.

Closed 2023-02-04.

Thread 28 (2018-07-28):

Structure Documentation

ghost, 2018-07-28:
We need to generate documentation for the structure of the system:

 - [ ] as a whole (base station, rover, communications equipment)
 - [ ] within the rover (raspberry Pi's, HATs, controllers)
 - [x] as ROS nodes

These may be combined/blurred some. This is not a one time task. We should probably have these for each milestone.

Talonj123, 2018-07-29:
An example of the output from rqt_graph. This was generated on my laptop (not the rover) so the actual input/output nodes are missing. That is why the `Drive_Board_Hardware` namespace only has the 6 channels used by the `Drivetrain_Ouptut` node.

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

Talonj123, 2018-07-30:
Here's the version generated from the rover when running. I set it to only show active topics, so the PWM drivers don't show all 16 channels.
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

Talonj123, 2018-07-30:
The only nodes that are not relocatable are the `*_Interface` nodes (relocating them breaks the base station interface) and the nodes in the `*_Board_HW` namespaces (relocating them requires re-wiring the rover. Everything else can be run on any board (functionally) As we get closet to a complete system, we will want to run CPU load analysis and see if any boards would benefit from re-balancing the system. We could go to a hardware-based division: Each board is responsible for a set of hardware (GPS, PWM, etc.) instead of each board handling the control of a single subsystem.

Talonj123, 2018-08-01:
Another Update:
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

Talonj123, 2018-08-01:
I would like to put this into visio, powerpoint, or draw.io - but it has been changing somewhat rapidly as I add new nodes. Once we get more into testing/bugfixing, it will be more stable.

Talonj123, 2018-08-01:
@jensenm7

Talonj123, 2018-08-03:
With some changes to the drive system:
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

Closed 2023-02-04.

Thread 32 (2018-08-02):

Camera Pan External Potentiometer

ghost, 2018-08-02:
The camera pan servo has had the potentiometer removed. In order to keep the zero-movement point from changing, we need to replace it with some hard-wired resistors, or just cover the shaft in epoxy.

Closed 2023-02-04.

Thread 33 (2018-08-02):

Skills we need

Talonj123, 2018-08-02:
Just a list of useful skills for the rover systems team (non-exhaustive):
 - Wiring:
   - Crimping
   - Soldering
   - Sheathing
   - Wire Sizing
 - Programming
   - Python
   - Sockets
   - ROS
 - Embedded (the connection between programming and hardware)
   - PWM
   - CAN/I2C/SPI buses
   - Power Management
   - Raspberry Pi
 - Radio
   - HAM License (someone in the base station needs to have)
   - Antenna selection
   - Range/penetration limitations of different bands

Closed 2018-10-03.

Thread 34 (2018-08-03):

Main camera

ghost, 2018-08-03:
It might be http://www.accessories-shops.com/sony-camera-series/cctv-sony-camera-zoom-module-fcb-ex45cp-colour.html

We do know it supports the VISCA protocol for commands like zooming in and out. None of the wires coming out of the camera are labeled/color coded, so we really don't want to have to redo those.

That is all I know.

Talonj123, 2018-08-06:
We think we found it: https://www.aegis-elec.com/media/wysiwyg/pdf/FCB-EX1010.compressed.pdf

Talonj123, 2018-08-09:
We have a 1.2 GHz trainmitter/receiver pair. I am concerned about the range though, we need to get it running (requires RCA cable) and do some testing.

Alternatively, we can switch to digital with adapter boards (price unknown).

Talonj123, 2018-08-09:
I have contacted stemmer about one of these boards, https://www.stemmer-imaging.co.uk/en/products/series/sony-fcb-interfaces/. We will see what details they can give us.

Talonj123, 2018-08-14:
As far as I can tell, we'll need one of these to provide power and get video out (I think we want the VBS pin for analog):
KYOCERA ELCO 00 6200 509 130 000+

Talonj123, 2018-08-15:
The board from above does not support our camera, but there is another one that might:
[Atomas-Mini-LVDS](http://imaging.ionodes.com/atomas-mini-lvds)

Talonj123, 2018-10-03:
I am trying to get a response from some sales people who think they can help

Closed 2023-02-04.

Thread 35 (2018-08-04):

New Components List

ghost, 2018-08-04:
# Things we need/want to get:
## Regulators (enhancement)
Our current regulators are a bit heavy and have unknown thermal characteristics.
Loads:
 - 1A per Pi + ~0.5 for HATs. I'd like to reserve 2A per Pi. 4 Pis => 8A @ 5V
 - 1.5 A peak/fan x 8 fans => 12A peak @ 12V, 6A continuous
 - Network switch rated for 1A @ 24V and switch 1A@12V, so total 3A @ 12V
 - Camera Servos 1.8A each => 3.6A @ 6V

I would like to keep all these separate.

## Sensors (mixed)
We need some additional sensors:
 - ADC for battery voltage (requirement)
 - [LiDAR](https://www.sparkfun.com/products/14032)/other reliable rangefinder (enhancement)
 - Current monitors for various power rails in the E-Box (see regulators section) and beyond (up to 60A combined for wheels, unknown for the arm). (enhancement)

## Actuators
 - Relay for Software E-Stop. Has to handle total E-box load (before regulators). Currently estimated at about 10.5A peak for a 22.2V battery (230W). (enhancement)
 - Screen of some sort (check rules to see if we can use one to leave messages for the field team). E-Ink should be visible in daylight. (enhancement
 - Lights/other indicators to indicate when we reach autonomous waypoints. (requirement, I think)

## Miscellaneous
 - 12V power rail for the arm
   - we could make another bus bar, but that might be overkill, a terminal block might be sufficient. I'd prefer to avoid a octopus cable if possible, though I could go for a sealed bar by the arm.
 - 2x Raspberry Pi 3B.
   - We need these for the science and arm board. It is possible to use just one since only one of those systems will be attached, but it makes everything more complicated.
 - [POE injectors for the RM5 and camera](https://www.amazon.com/iCreatin-Passive-Injector-Splitter-Connector/dp/B00NRHNPUA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)

Talonj123, 2018-08-05:
Some regulator options:
 - [Our current ones](https://www.aliexpress.com/item/DC-Adjustable-Voltage-Regulator-Module-DC-4-5-30V-to-0-8-30V-12A-Buck-Converters/1724570414.html)
   - Price/Amp: $0.75
   - Weight: ???
 - [KNACRO unit](https://www.amazon.com/KNACRO-Waterproof-Converter-Regulator-Transformer/dp/B073XCC1GR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)
   - Price/amp: $1.06
   - Weight: 60g
   - Sealed: yes
 - [BINZET unit](https://www.amazon.com/BINZET-Converter-Regulator-Regulated-Transformer/dp/B00J3MHTYG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)
   - Price/Amp: $1.10
   - Weight: ???
   - Sealed: yes

Talonj123, 2018-08-08:
ADC Options:
 - [12-bit 4-channel breakout board](https://learn.adafruit.com/raspberry-pi-analog-to-digital-converters/ads1015-slash-ads1115)
   - Python Library: Yes

Closed 2023-02-04.

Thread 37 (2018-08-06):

E-Box Rear Fans power cable problem

Talonj123, 2018-08-06:
There are 200 Ohms between the fan cable connector and the terminal block. As we are planning to replace the E-Box mounting plate, I would prefer to wait to take the E-Box apart to debug this until we do it for the new mounting.

Talonj123, 2018-08-09:
I resoldered the cables (I tried to solder up the wires a bit for strain relief) and it works now - 0.2 ohms.

Closed 2018-08-09.

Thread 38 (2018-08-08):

Regulator Rails

ghost, 2018-08-08:
# Discussion/record about splitting up what components are supplied by what regulators
See #35 for discussion of specific regulator options.

## Proposal 1 - All sealed, fixed-voltage units
### Components
 - Pi Power: [KNACRO unit](https://www.amazon.com/KNACRO-Waterproof-Converter-Regulator-Transformer/dp/B073XCC1GR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)
 - Switch and RM5: [GEREE](https://www.amazon.com/GEREE-Converter-Module-15-35v-adapter/dp/B00O6S4QO8/)
 - Fans, Cameras, Status Light Pole: [12V 20A regulators ("our other current ones")](https://www.amazon.com/Nextrox-Converter-Regulator-Step-Down/dp/B00BWKXTUU)
 - Arm: [12V 20A regulators ("our other current ones")](https://www.amazon.com/Nextrox-Converter-Regulator-Step-Down/dp/B00BWKXTUU)
 - Camera Servos: [Awaking unit](https://www.amazon.com/Aweking-Waterproof-Converter-Regulator-Transformer/dp/B06W9MZJ8W/)

### Summary
 - Cost: $76
   - Minus Owned: $38
 - Weight: 0.872 kg
 - Advantages:
   - All sealed, simplifies mounting (can go on the bottom or outside the E-Box)
 - Disadvantages:
   - Heavier than absolutely necessary.

Closed 2023-02-04.

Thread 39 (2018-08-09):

Arm wiring

ghost, 2018-08-09:
Once the arm is built, we need it wired. It should be just adding an XT-60 out of the E-Box and wiring that to an octopus cable (one end for each motor) the split cables need to handle some current so probably go with 12 or 14 AWG wire. Use some sheathing or heatshrink to pair the + and - wires of each connector. It looks like the motor controllers will go at the base of the arm, so add cables from there to the motors and put connectors to the motors.

Closed 2023-02-04.

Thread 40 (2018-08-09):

Spending

ghost, 2018-08-09:
In addition to #35.

 - [Li-Ion one](http://www.batterysupports.com/22v-252v-1818650-7800mah-6s3p-lithium-ion-liion-battery-pack-p-141.html)
   - $85
   - Should have 2 available for charging one while the other is in use.

- Lighter material for the E-box (not big as most of the weight is from other stuff)

Talonj123, 2018-08-09:
@GageLochner

Closed 2023-02-04.

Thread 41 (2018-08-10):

Battery Sharing

ghost, 2018-08-10:
We may want to put the switch, antenna, and cameras on a shared line with both batteries. The simplest method is to put a diode from each battery to the shared line, preventing conflicts when both are active. Here is a diode that should do the trick (it's rated to handle the whole E-Box, just to be safe and allow more flexibility):
https://www.digikey.com/product-detail/en/stmicroelectronics/FERD2045SB-TR/497-18030-1-ND/8570660

Closed 2023-02-04.

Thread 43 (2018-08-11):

Antennas

ghost, 2018-08-11:
Depending on the results of range tests, we may need to look into other antenna systems. With point-to-point line-of-sight operation, the RM5 transceivers can go up to at least 70 km with parabolic antennas.

Talonj123, 2018-10-03:
Sector antenna option (3x range boost?):
https://store.ubnt.com/collections/wireless/products/5ghz-airmax-basestation-19dbi-120-deg-rocket-kit

Closed 2023-02-04.

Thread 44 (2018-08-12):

Required Equipment Checklist

ghost, 2018-08-12:
We should have a list of the equipment we need to have to operate the rover. This does not include equipment on the rover itself, just the base station.

# Base Station
 - RM5
 - POE Injector
   - 4-6S Battery required if an outlet is not available
   - breakout cable required if an outlet is not available
    - We cold buy a DC-input POE injector
 - Long Ethernet cable (with coupler if using a POE breakout cable)
 - Joystick/Controller
 - SMA Male-Male Connector for the antenna extension line (1.2 GHz camera analog reciever)

Closed 2023-02-04.

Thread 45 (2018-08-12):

1.2 GHz Video Transmitter

ghost, 2018-08-12:
The transmitter was run off of 18V or so last time we went to competition, it is rated for 12. It gets really hot, even with a heatsink, which could be because of damage.

Talonj123, 2018-10-03:
We can replace [the pair](https://www.amazon.com/Hikity-Updated-Wireless-Transmitter-Receiver/dp/B073Y1LKZG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) for $60 (same units) or get a [3W version](https://www.amazon.com/SainSonic-2-4GHz-Wireless-Transmitter-Receiver/dp/B00G4S2CR6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) (old is 2W) for 77$

Closed 2023-02-04.

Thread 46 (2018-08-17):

LiDAR sensor

ghost, 2018-08-17:
This may be a Strategy team item. We have obtained a [LiDAR scanner](http://www.hizook.com/files/publications/HokuyoURG_Datasheet.pdf). It does not power from the USB, so any testing will require the main connector for power. The USB should enumerate as a serial port when it is powered and connected.

Closed 2023-02-04.

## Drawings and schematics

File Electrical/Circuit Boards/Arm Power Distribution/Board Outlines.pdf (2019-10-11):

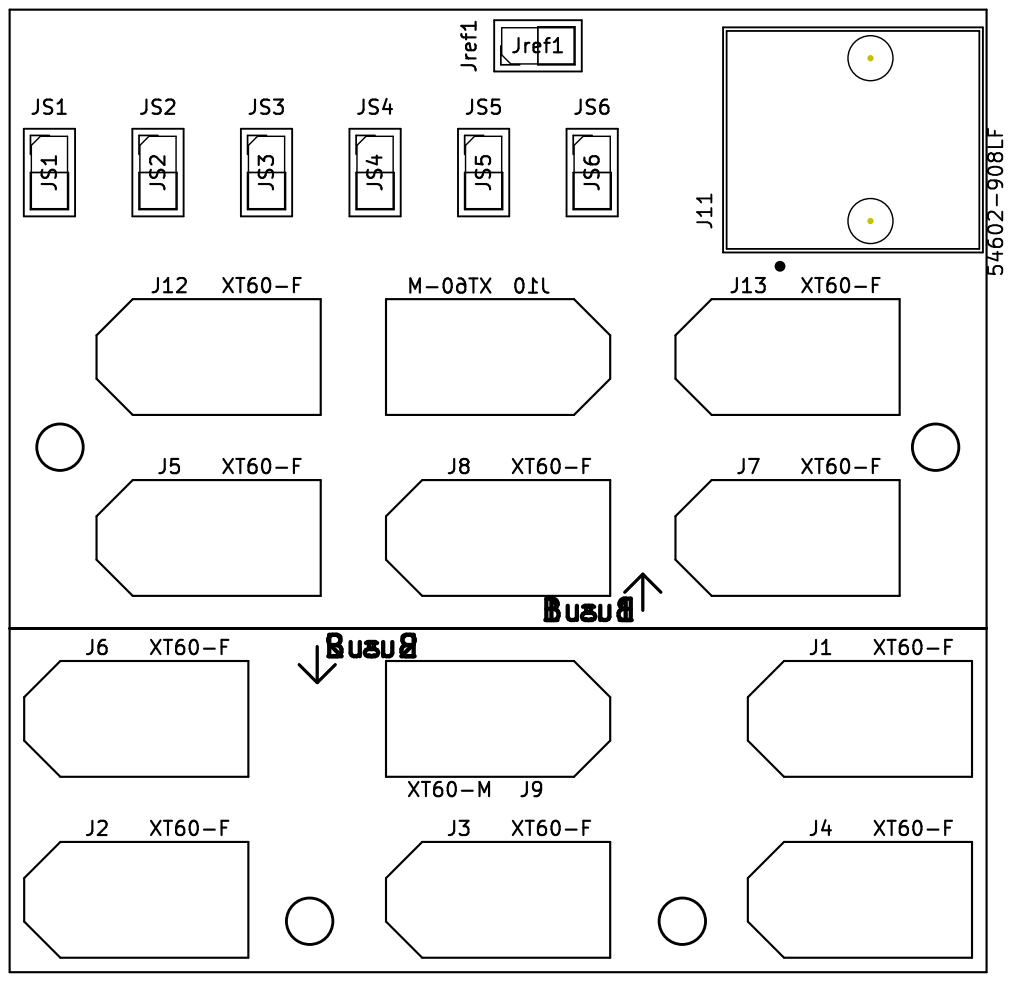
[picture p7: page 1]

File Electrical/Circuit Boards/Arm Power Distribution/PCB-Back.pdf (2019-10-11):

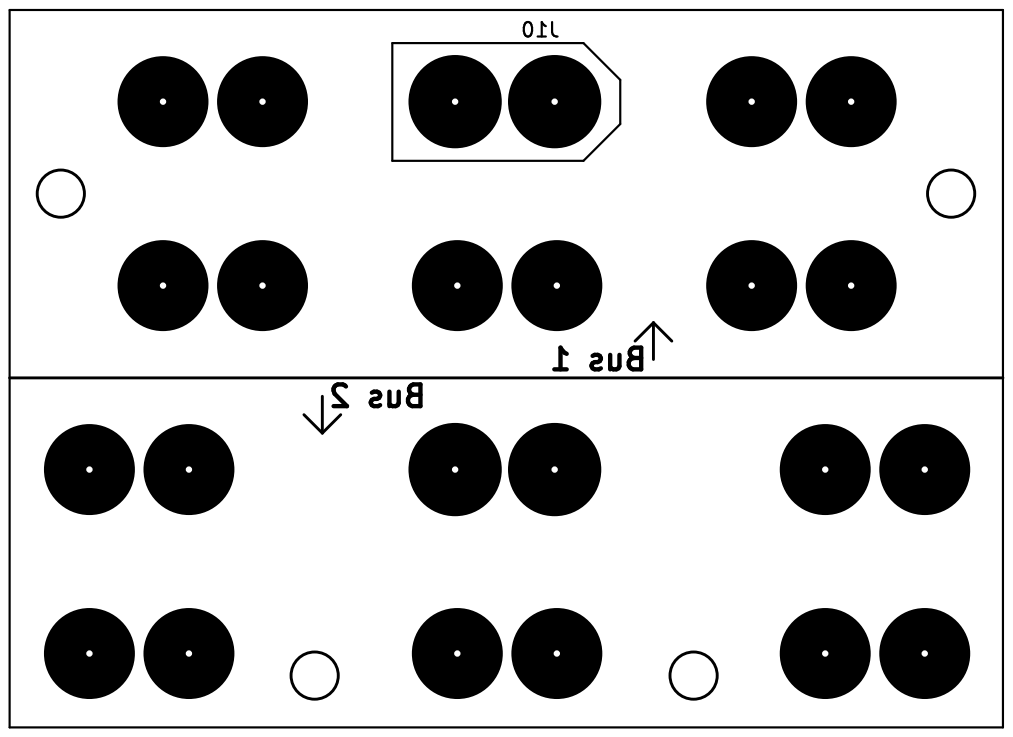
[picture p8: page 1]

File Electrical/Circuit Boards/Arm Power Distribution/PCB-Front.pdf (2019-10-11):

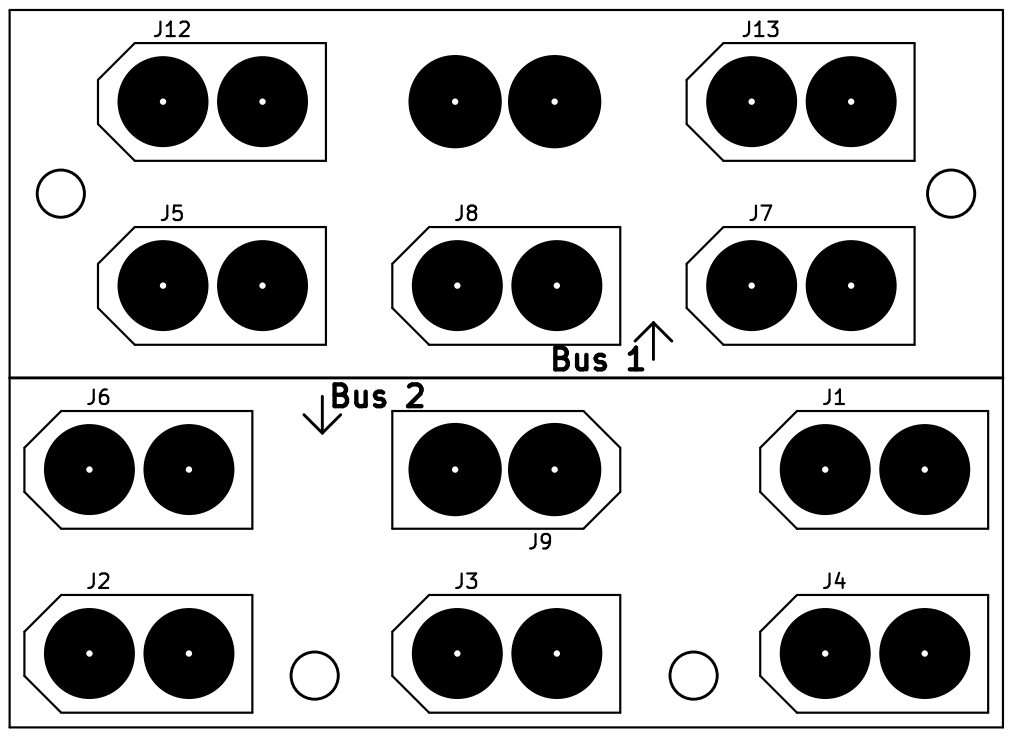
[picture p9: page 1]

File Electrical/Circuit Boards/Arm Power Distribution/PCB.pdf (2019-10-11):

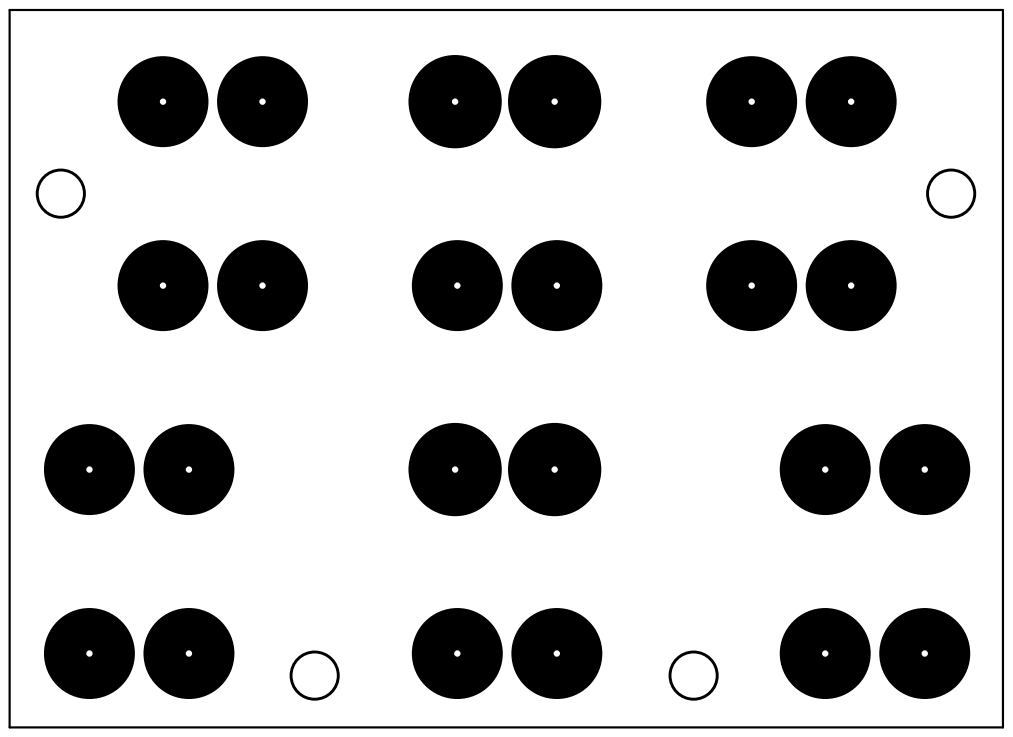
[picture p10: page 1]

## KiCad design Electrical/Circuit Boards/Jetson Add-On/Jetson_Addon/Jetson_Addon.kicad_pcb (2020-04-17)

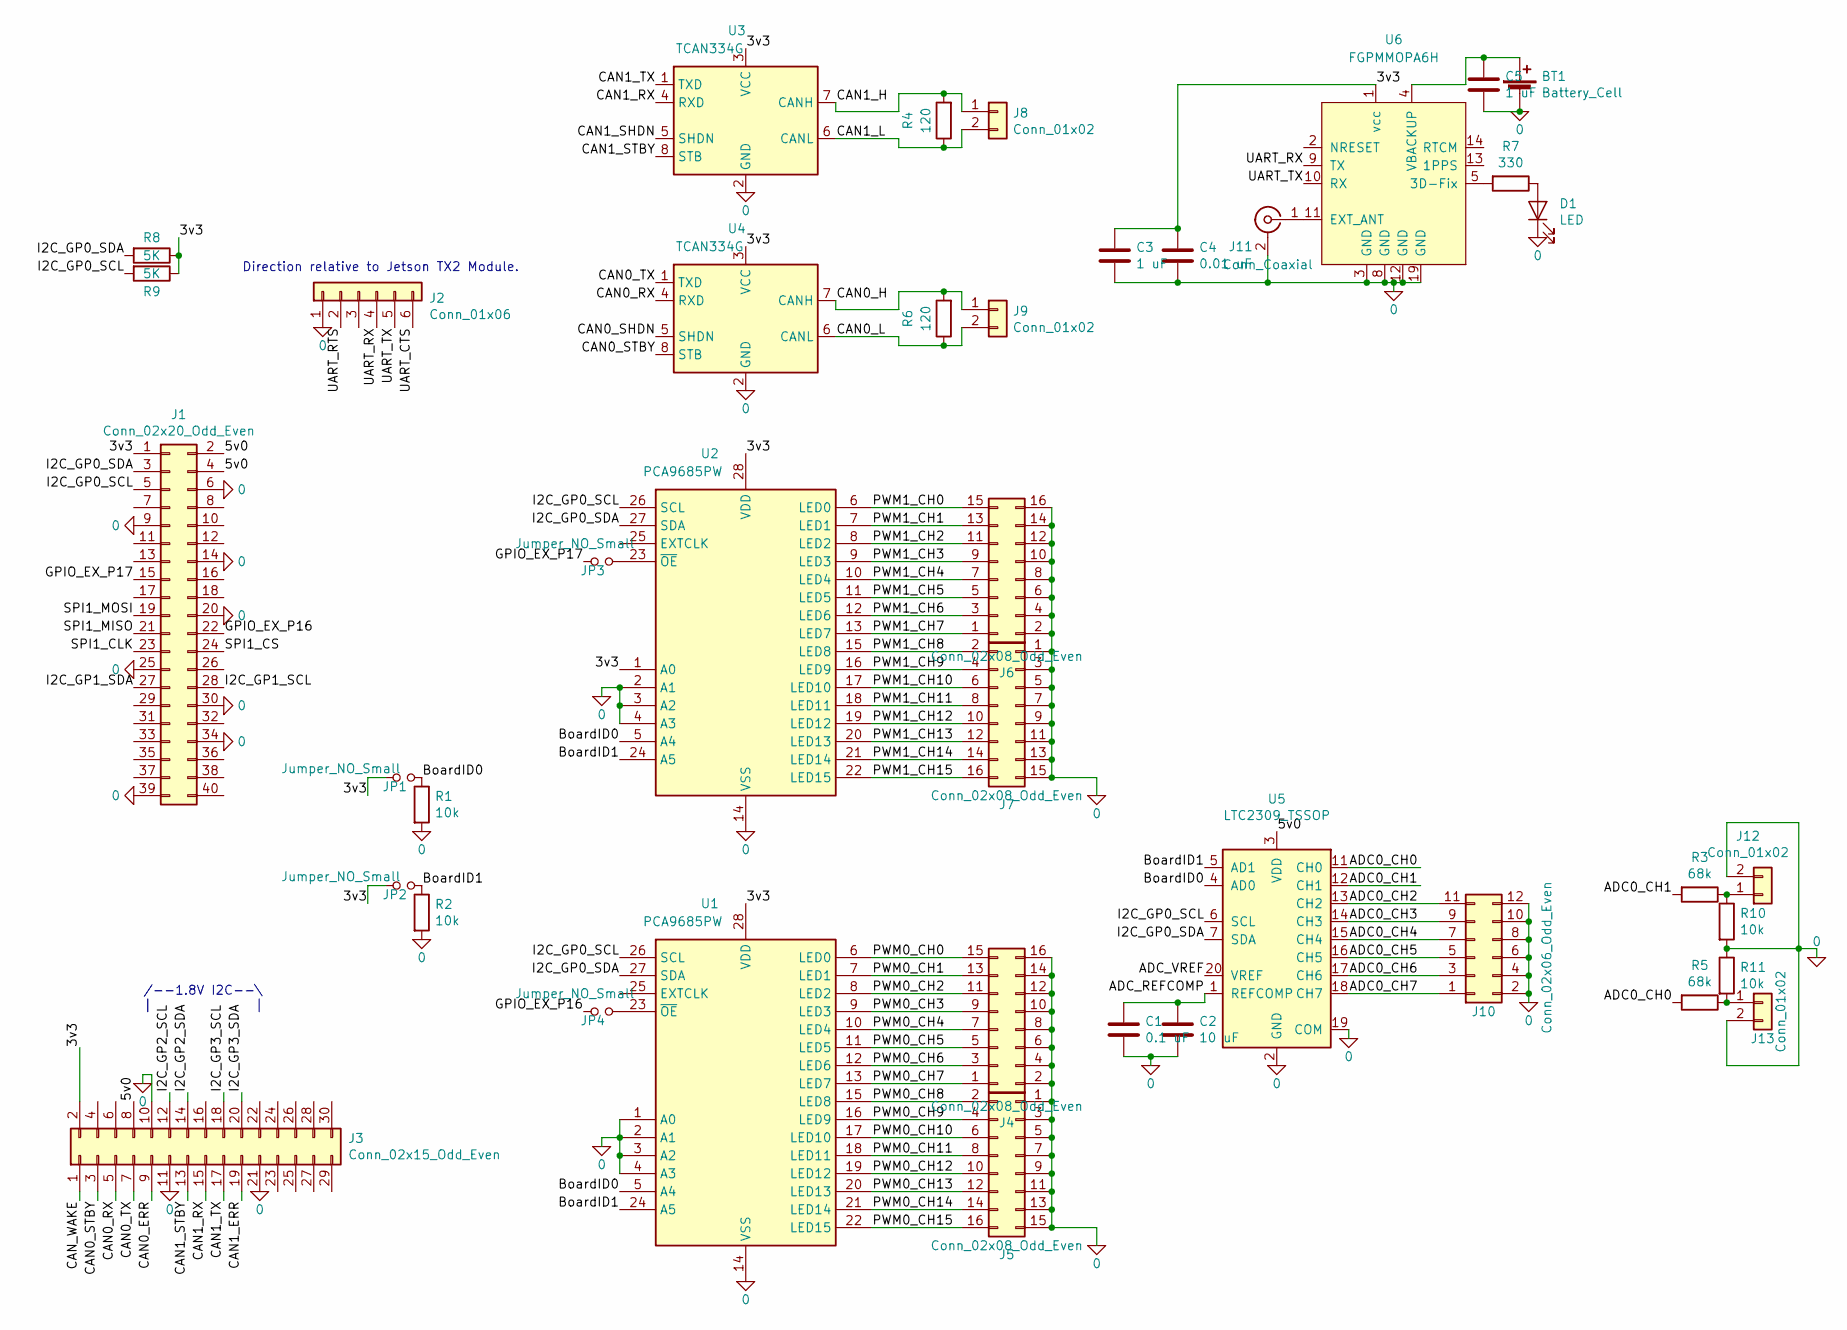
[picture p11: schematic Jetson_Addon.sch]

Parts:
BT1: Battery_Cell; BatteryHolder_Keystone_3000_1x12mm
C1: 0.1 uF; C_1206_3216Metric
C2: 10 uF; C_1206_3216Metric
C3, C5: 1 uF; C_0805_2012Metric
C4: 0.01 uF; C_0805_2012Metric
D1: LED; LED_1206_3216Metric
J1: Conn_02x20_Odd_Even; PinHeader_2x20_P2.54mm_Vertical
J2: Conn_01x06; PinHeader_1x06_P2.54mm_Vertical
J3: Conn_02x15_Odd_Even; PinHeader_2x15_P2.54mm_Vertical
J4, J5, J7: Conn_02x08_Odd_Even; PinHeader_2x08_P2.54mm_Vertical
J6: Conn_02x08_Odd_Even; PinHeader_2x08_P2.54mm_Horizontal
J8, J9, J12, J13: Conn_01x02; PinHeader_1x02_P2.54mm_Horizontal
J10: Conn_02x06_Odd_Even; PinHeader_2x06_P2.54mm_Horizontal
J11: Conn_Coaxial; SMA_Amphenol_132203-12_Horizontal
JP1, JP2, JP3, JP4: Jumper_NO_Small; SolderJumper-2_P1.3mm_Open_RoundedPad1.0x1.5mm
R1, R2, R10, R11: 10k; R_0805_2012Metric
R3, R5: 68k; R_0805_2012Metric
R4, R6: 120; R_0805_2012Metric
R7: 330; R_0805_2012Metric
R8, R9: 5K; R_0805_2012Metric
U1, U2: PCA9685PW; TSSOP-28_4.4x9.7mm_P0.65mm
U3, U4: TCAN334G; TSOT-23-8
U5: LTC2309_TSSOP; TSSOP-20_4.4x6.5mm_P0.65mm
U6: FGPMMOPA6H

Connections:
0: BT1.2 (-), C1.2, C2.2, C3.2, C4.2, C5.2, D1.1 (K), J1.6, J1.9, J1.14, J1.20, J1.25, J1.30, J1.34, J1.39, J2.1, J3.10, J3.11, J3.21, J4.2, J4.4, J4.6, J4.8, J4.10, J4.12, J4.14, J4.16, J5.1, J5.3, J5.5, J5.7, J5.9, J5.11, J5.13, J5.15, J6.2, J6.4, J6.6, J6.8, J6.10, J6.12, J6.14, J6.16, J7.1, J7.3, J7.5, J7.7, J7.9, J7.11, J7.13, J7.15, J10.2, J10.4, J10.6, J10.8, J10.10, J10.12, J11.2 (Ext), J12.2, J13.2, R1.2, R2.2, R10.2, R11.1, U1.1 (A0), U1.2 (A1), U1.3 (A2), U1.4 (A3), U1.14 (VSS), U2.2 (A1), U2.3 (A2), U2.4 (A3), U2.14 (VSS), U3.2 (GND), U4.2 (GND), U5.2 (GND), U5.8 (GND), U5.9 (GND), U5.19 (COM), U6.3 (GND), U6.8 (GND), U6.12 (GND), U6.19 (GND)
/3v3: C3.1, C4.1, J1.1, J3.2, JP1.1, JP2.1, R8.1, R9.1, U1.28 (VDD), U2.1 (A0), U2.28 (VDD), U3.3 (VCC), U4.3 (VCC), U6.1 (vcc)
/5v0: J1.2, J1.4, J3.8, U5.3 (VDD), U5.10 (VDD)
/ADC0_CH0: R5.2, U5.11 (CH0)
/ADC0_CH1: R3.2, U5.12 (CH1)
/ADC0_CH2: J10.11, U5.13 (CH2)
/ADC0_CH3: J10.9, U5.14 (CH3)
/ADC0_CH4: J10.7, U5.15 (CH4)
/ADC0_CH5: J10.5, U5.16 (CH5)
/ADC0_CH6: J10.3, U5.17 (CH6)
/ADC0_CH7: J10.1, U5.18 (CH7)
/ADC_REFCOMP: C1.1, C2.1, U5.1 (REFCOMP)
/ADC_VREF: U5.20 (VREF)
/BoardID0: JP1.2, R1.1, U1.5 (A4), U2.5 (A4), U5.4 (AD0)
/BoardID1: JP2.2, R2.1, U1.24 (A5), U2.24 (A5), U5.5 (AD1)
/CAN0_ERR: J3.9
/CAN0_H: J9.1, R6.2, U4.7 (CANH)
/CAN0_L: J9.2, R6.1, U4.6 (CANL)
/CAN0_RX: J3.5, U4.4 (RXD)
/CAN0_SHDN: U4.5 (SHDN)
/CAN0_STBY: J3.3, U4.8 (STB)
/CAN0_TX: J3.7, U4.1 (TXD)
/CAN1_ERR: J3.19
/CAN1_H: J8.1, R4.2, U3.7 (CANH)
/CAN1_L: J8.2, R4.1, U3.6 (CANL)
/CAN1_RX: J3.15, U3.4 (RXD)
/CAN1_SHDN: U3.5 (SHDN)
/CAN1_STBY: J3.13, U3.8 (STB)
/CAN1_TX: J3.17, U3.1 (TXD)
/CAN_WAKE: J3.1
/GPIO_EX_P16: J1.22, JP4.1
/GPIO_EX_P17: J1.15, JP3.1
/I2C_GP0_SCL: J1.5, R9.2, U1.26 (SCL), U2.26 (SCL), U5.6 (SCL)
/I2C_GP0_SDA: J1.3, R8.2, U1.27 (SDA), U2.27 (SDA), U5.7 (SDA)
/I2C_GP1_SCL: J1.28
/I2C_GP1_SDA: J1.27
/I2C_GP2_SCL: J3.12
/I2C_GP2_SDA: J3.14
/I2C_GP3_SCL: J3.18
/I2C_GP3_SDA: J3.20
/PWM0_CH0: J4.15, U1.6 (LED0)
/PWM0_CH1: J4.13, U1.7 (LED1)
/PWM0_CH2: J4.11, U1.8 (LED2)
/PWM0_CH3: J4.9, U1.9 (LED3)
/PWM0_CH4: J4.7, U1.10 (LED4)
/PWM0_CH5: J4.5, U1.11 (LED5)
/PWM0_CH6: J4.3, U1.12 (LED6)
/PWM0_CH7: J4.1, U1.13 (LED7)
/PWM0_CH8: J5.2, U1.15 (LED8)
/PWM0_CH9: J5.4, U1.16 (LED9)
/PWM0_CH10: J5.6, U1.17 (LED10)
/PWM0_CH11: J5.8, U1.18 (LED11)
/PWM0_CH12: J5.10, U1.19 (LED12)
/PWM0_CH13: J5.12, U1.20 (LED13)
/PWM0_CH14: J5.14, U1.21 (LED14)
/PWM0_CH15: J5.16, U1.22 (LED15)
/PWM1_CH0: J6.15, U2.6 (LED0)
/PWM1_CH1: J6.13, U2.7 (LED1)
/PWM1_CH2: J6.11, U2.8 (LED2)
/PWM1_CH3: J6.9, U2.9 (LED3)
/PWM1_CH4: J6.7, U2.10 (LED4)
/PWM1_CH5: J6.5, U2.11 (LED5)
/PWM1_CH6: J6.3, U2.12 (LED6)
/PWM1_CH7: J6.1, U2.13 (LED7)
/PWM1_CH8: J7.2, U2.15 (LED8)
/PWM1_CH9: J7.4, U2.16 (LED9)
/PWM1_CH10: J7.6, U2.17 (LED10)
/PWM1_CH11: J7.8, U2.18 (LED11)
/PWM1_CH12: J7.10, U2.19 (LED12)
/PWM1_CH13: J7.12, U2.20 (LED13)
/PWM1_CH14: J7.14, U2.21 (LED14)
/PWM1_CH15: J7.16, U2.22 (LED15)
/SPI1_CLK: J1.23
/SPI1_CS: J1.24
/SPI1_MISO: J1.21
/SPI1_MOSI: J1.19
/UART_CTS: J2.6
/UART_RTS: J2.2
/UART_RX: J2.4, U6.9 (TX)
/UART_TX: J2.5, U6.10 (RX)
unnamed: BT1.1 (+), C5.1, U6.4 (VBACKUP)
unnamed: D1.2 (A), R7.1
unnamed: J11.1 (In), U6.11 (EXT_ANT)
unnamed: J12.1, R3.1, R10.1
unnamed: J13.1, R5.1, R11.2
unnamed: JP3.2, U2.23 (~OE)
unnamed: JP4.2, U1.23 (~OE)
unnamed: R7.2, U6.5 (3D-Fix)

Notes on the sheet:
/--1.8V I2C--\ | |
Direction relative to Jetson TX2 Module.

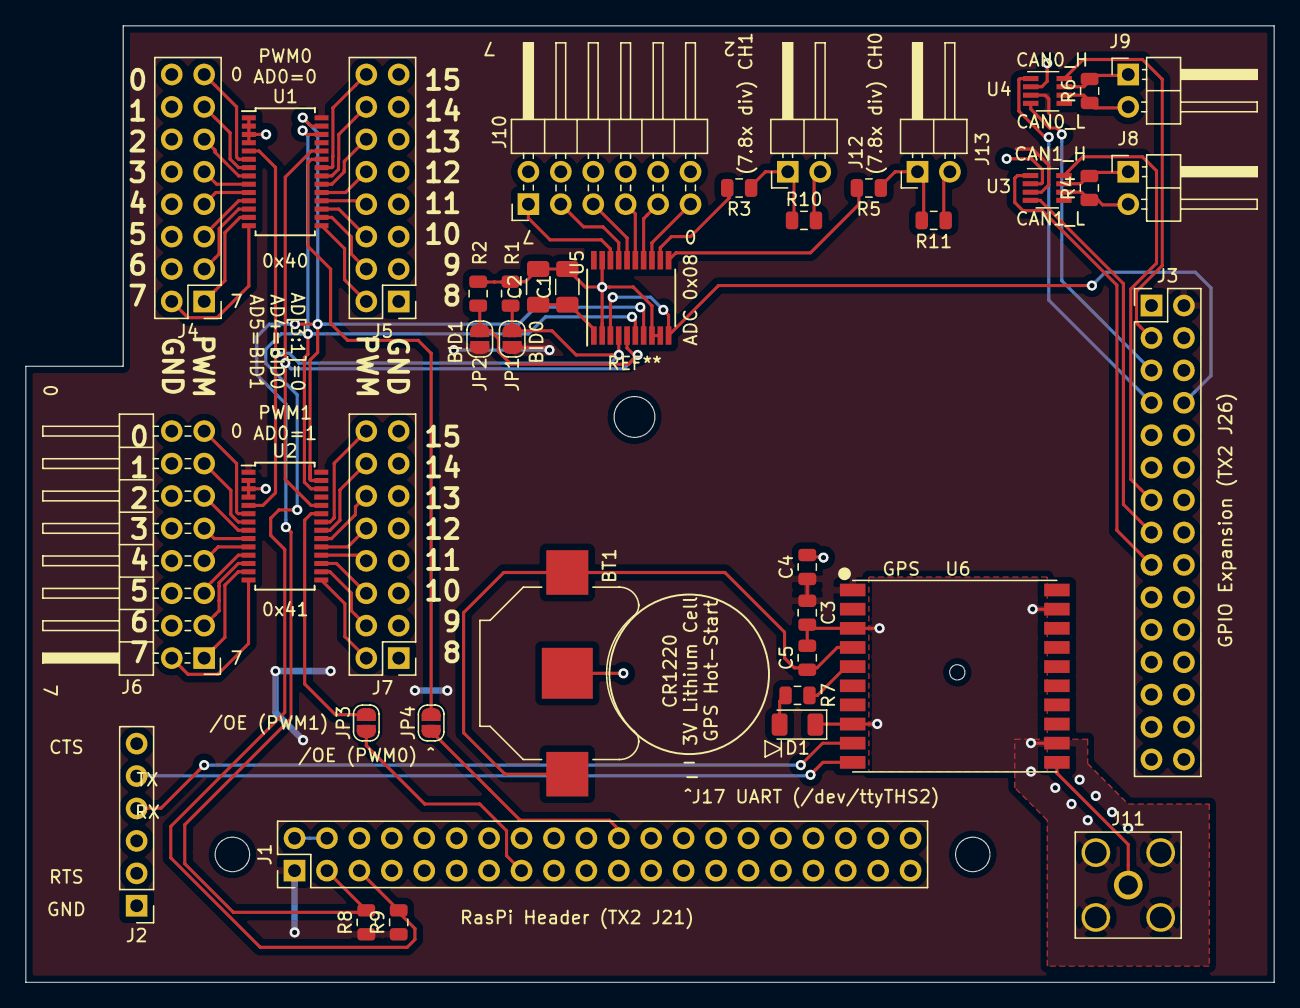
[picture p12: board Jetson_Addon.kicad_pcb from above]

Board: 2 copper layers, 97.8 x 74.9 mm, 41 parts (0 on the bottom side), 70 nets.

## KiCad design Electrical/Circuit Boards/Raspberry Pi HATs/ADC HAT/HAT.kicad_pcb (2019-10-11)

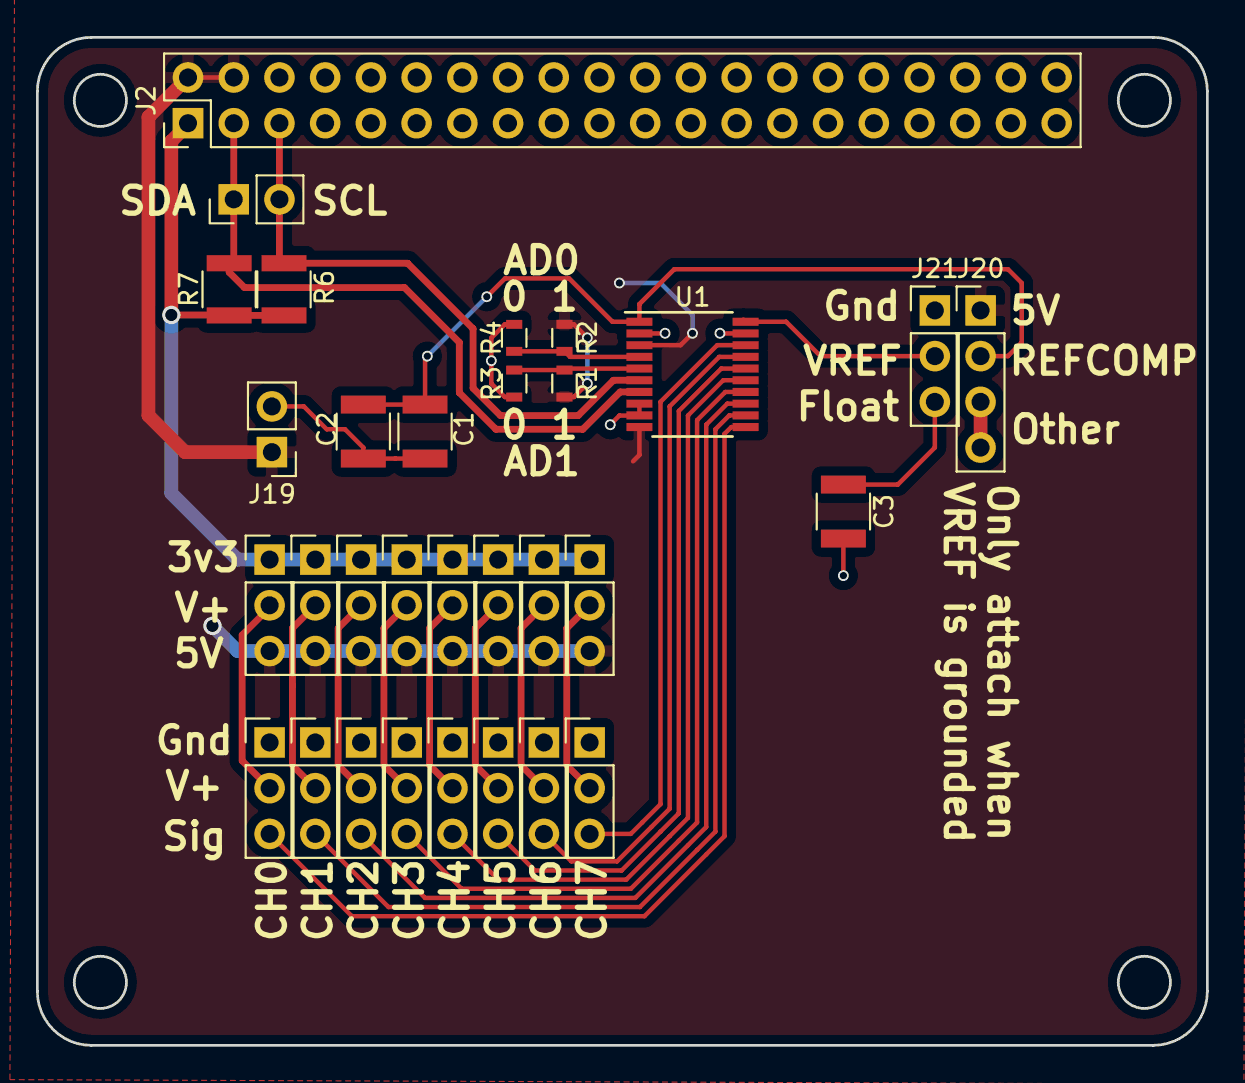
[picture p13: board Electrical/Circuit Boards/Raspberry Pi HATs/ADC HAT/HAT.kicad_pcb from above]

Board: 2 copper layers, 65.0 x 56.0 mm, 31 parts (0 on the bottom side), 27 nets.

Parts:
C1: 0.1 uF; C_1210
C2: 10 uF; C_1210
C3: 2.2 uF; C_1210
J1, J19: CONN_01X02; Pin_Header_Straight_1x02_Pitch2.54mm
J2: CONN_02X20; Pin_Header_Straight_2x20_Pitch2.54mm
J3, J4, J5, J6, J7, J8, J9, J10, J11, J12, J13, J14, J15, J16, J17, J18: CONN_01X03; Pin_Header_Straight_1x03_Pitch2.54mm
J20: CONN_01X04_MALE; Pin_Header_Straight_1x04_Pitch2.54mm
J21: CONN_01X03_MALE; Pin_Header_Straight_1x03_Pitch2.54mm
R1, R2, R3, R4: 0; R_0603
R6, R7: 2.2K; R_1210
U1: LTC2309_TSSOP; TSSOP-20_4.4x6.5mm_Pitch0.65mm

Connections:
+3V3: J2.1, J2.17, J3.1, J4.1, J5.1, J6.1, J7.1, J8.1, J9.1, J10.1, R6.1, R7.1
+5V: J2.2, J2.4, J3.3, J4.3, J5.3, J6.3, J7.3, J8.3, J9.3, J10.3, J19.1, J20.1, R1.1, R2.1, U1.3, U1.10
/A0: J11.3, U1.11
/A1: J12.3, U1.12
/A2: J13.3, U1.13
/A3: J14.3, U1.14
/A4: J15.3, U1.15
/A5: J16.3, U1.16
/A6: J17.3, U1.17
/A7: J18.3, U1.18
/SCL: J1.2, J2.5, R6.2, U1.6
/SDA: J1.1, J2.3, R7.2, U1.7
GND: C1.2, C2.2, C3.2, J2.6, J2.9, J2.14, J2.20, J2.25, J2.30, J2.34, J2.39, J11.1, J12.1, J13.1, J14.1, J15.1, J16.1, J17.1, J18.1, J19.2, J21.1, R3.1, R4.1, U1.2, U1.8, U1.9, U1.19
unnamed: C1.1, C2.1, J20.2, U1.1
unnamed: C3.1, J21.3
unnamed: J10.2, J18.2
unnamed: J3.2, J11.2
unnamed: J4.2, J12.2
unnamed: J5.2, J13.2
unnamed: J6.2, J14.2
unnamed: J7.2, J15.2
unnamed: J8.2, J16.2
unnamed: J9.2, J17.2
unnamed: J20.3, J20.4
unnamed: J21.2, U1.20
unnamed: R1.2, R3.2, U1.5
unnamed: R2.2, R4.2, U1.4

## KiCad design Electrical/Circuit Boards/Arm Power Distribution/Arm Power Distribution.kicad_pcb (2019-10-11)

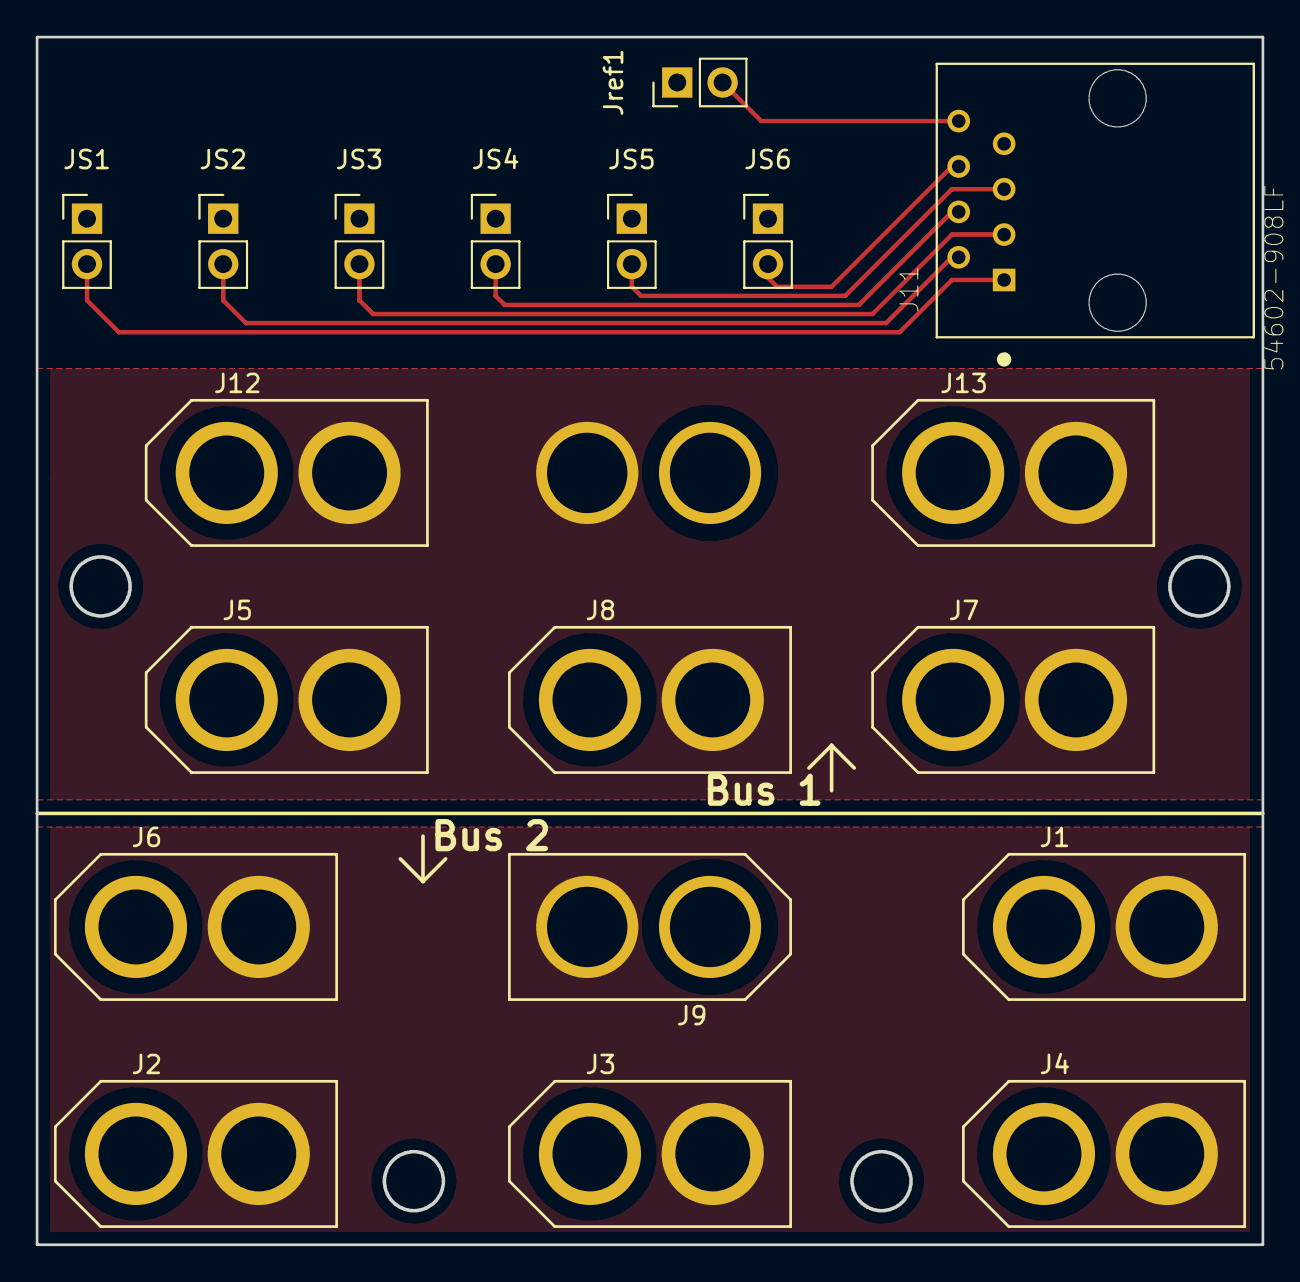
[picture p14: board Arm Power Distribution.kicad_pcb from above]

Board: 2 copper layers, 68.6 x 67.6 mm, 20 parts (1 on the bottom side), 12 nets.

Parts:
J1, J2, J3, J4, J5, J6, J7, J8, J12, J13: XT60-F
J9, J10: XT60-M
J11: 54602-908LF; AMPHENOL_54602-908LF
JS1, JS2, JS3, JS4, JS5, JS6: CONN_01X02_MALE; Pin_Header_Straight_1x02_Pitch2.54mm
Jref1: CONN_01X02_MALE; Pin_Header_Straight_1x02_Pitch2.54mm

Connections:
/HP0: J5.1, J7.1, J8.1, J10.1, J12.1, J13.1
/HP22: J5.2, J7.2, J8.2, J10.2, J12.2, J13.2
/LP0: J1.1, J2.1, J3.1, J4.1, J6.1, J9.1
/LP12: J1.2, J2.2, J3.2, J4.2, J6.2, J9.2
unnamed: J11.1, JS1.2
unnamed: J11.2, JS2.2
unnamed: J11.3, JS3.2
unnamed: J11.4, JS4.2
unnamed: J11.5, JS5.2
unnamed: J11.6, JS6.2
unnamed: J11.7, JS1.1, JS2.1, JS3.1, JS4.1, JS5.1, JS6.1, Jref1.1
unnamed: J11.8, Jref1.2

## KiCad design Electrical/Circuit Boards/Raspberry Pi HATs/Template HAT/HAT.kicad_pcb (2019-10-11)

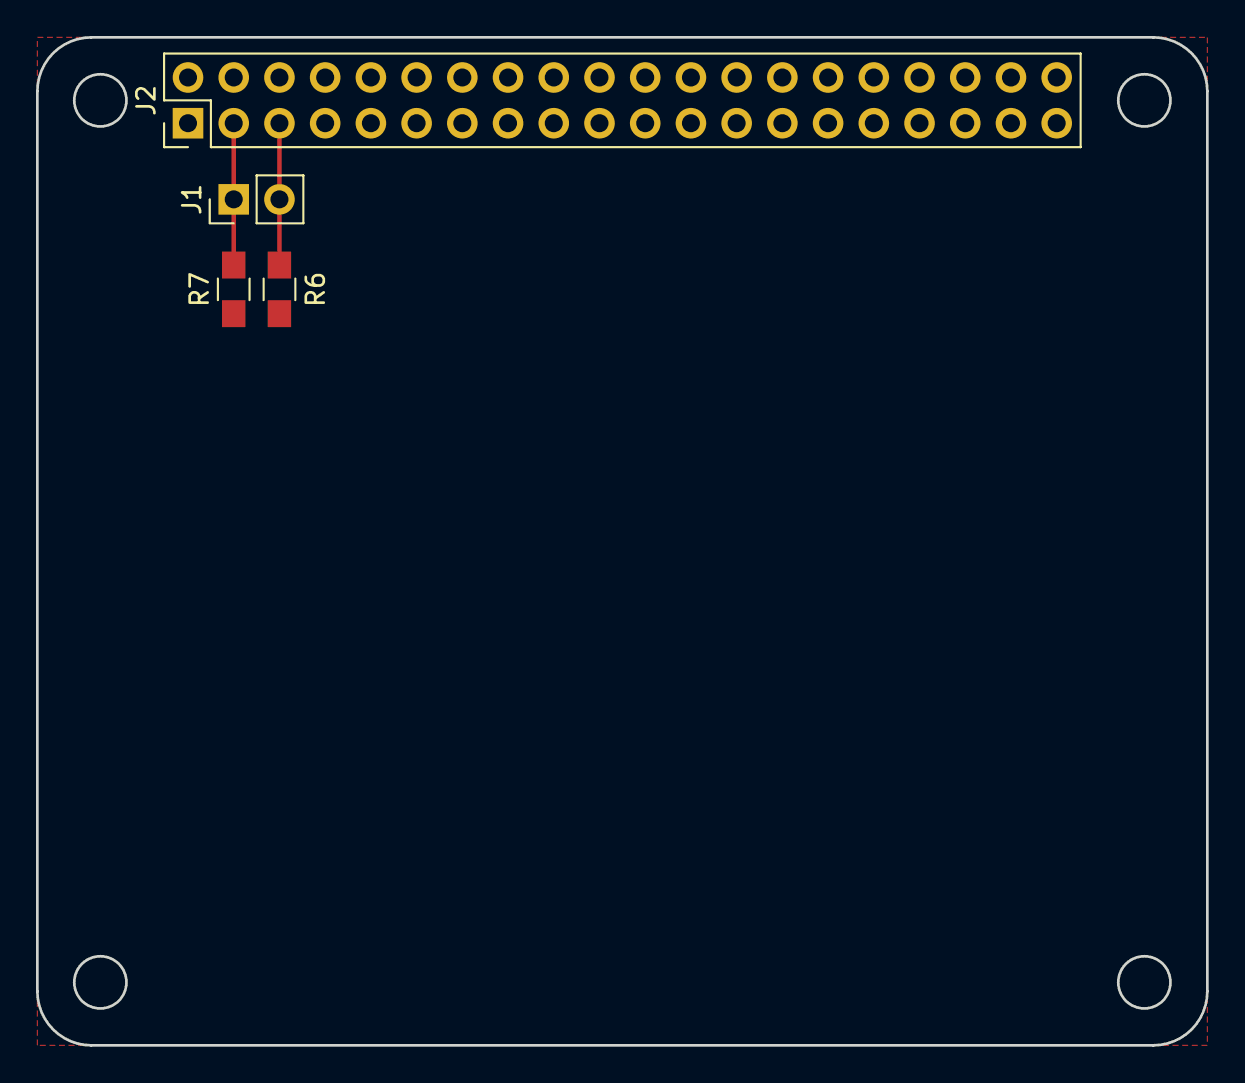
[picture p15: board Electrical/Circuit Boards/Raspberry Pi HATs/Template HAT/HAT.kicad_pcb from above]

Board: 2 copper layers, 65.0 x 56.0 mm, 4 parts (0 on the bottom side), 5 nets.

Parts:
J1: CONN_01X02; Pin_Header_Straight_1x02_Pitch2.54mm
J2: CONN_02X20; Pin_Header_Straight_2x20_Pitch2.54mm
R6, R7: 2.2K; R_0805_HandSoldering

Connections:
+3V3: J2.1, J2.17, R6.1, R7.1
+5V: J2.2, J2.4
/SCL: J1.2, J2.5, R6.2
/SDA: J1.1, J2.3, R7.2
GND: J2.6, J2.9, J2.14, J2.20, J2.25, J2.30, J2.34, J2.39

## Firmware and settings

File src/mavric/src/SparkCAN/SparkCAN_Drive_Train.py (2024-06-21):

#!/usr/bin/env python3
'''
Description: Reads arm and Drive topics and controlls the relevant motors
Author: Jacob Peskuski, Gabe Carlson, Nathan Logston

Topics:
    Publishers:
        SteerPosition
        JointPosition
        JointVelocity
    Subscribers:
        Drive_Train
        Steer_Train
        Drive_Sensitivity
        ShoulderPitch
        ShoulderRot
        ElbowPitch
        WristPitch
        WristRot
        Arm_Sensitivity
'''

import rospy
from std_msgs.msg import Float64
from mavric.msg import Steer, Drivetrain, Steertrain, ArmData
from SparkCAN import SparkBus


# Drive Scales
c_Scale_Max = 1.2*20
c_Scale = c_Scale_Max
c_str_Scale = 0.15
# Arm Scales
c_ShoulderPitch = 1         # Define individual arm rates
c_ShoulderRot = 1           # If one axis is faster/slower than the others, change these values
c_ElbowPitch = 1
c_WristPitch = 1
c_WristRot = 1
# Science Scales
c_Drill = 1
c_DrillActuator = 1

# Drive Directions
c_lfDir = 1
c_lmDir = 1
c_lbDir = 1
c_rfDir = -1
c_rmDir = -1
c_rbDir = -1
c_str_lfDir = 1
c_str_lbDir = 1
c_str_rfDir = 1
c_str_rbDir = 0.9
# Arm Directions
c_ShoulderRotDir = 1        
c_ShoulderPitchDir = 1     # If axis is moving wrong way, invert these 
c_ElbowPitchDir = -1
c_WristPitchDir = -1
c_WristRotDir = 1
# Science Directions
c_DrillDir = -1
c_DrillActuatorDir = 1

#set up globals for spark outputs. These should be zero
lf = 0
lm = 0
lb = 0
rf = 0
rm = 0
rb = 0
slf = 0
slb = 0
srf = 0
srb = 0
ShoulderRot = 0
ShoulderPitch = 0
ElbowPitch = 0
WristPitch = 0
WristRot = 0
Drill = 0
DrillActuator = 0


# Setup Sparkmax on can bus
sparkBus = SparkBus(channel="can0", bustype='socketcan', bitrate=1000000)
# Wheels
spark_lf = sparkBus.init_controller(1)
spark_lm = sparkBus.init_controller(2)
spark_lb = sparkBus.init_controller(3)
spark_rf = sparkBus.init_controller(4)
spark_rm = sparkBus.init_controller(5)
spark_rb = sparkBus.init_controller(6)
# Steering
spark_str_lf = sparkBus.init_controller(7)
spark_str_lb = sparkBus.init_controller(8)
spark_str_rf = sparkBus.init_controller(9)
spark_str_rb = sparkBus.init_controller(10)
# Arm
spark_shoulderPitch = sparkBus.init_controller(11)
spark_shoulderRot = sparkBus.init_controller(12)
spark_elbowPitch = sparkBus.init_controller(13)
spark_wristPitch = sparkBus.init_controller(14)
spark_wristRot = sparkBus.init_controller(15)
# Science
spark_Drill = sparkBus.init_controller(16)
spark_DrillActuator = sparkBus.init_controller(17)


# Axis Feedback Publishers
def strpub():
  steerMsg = Steer()
  steerMsg.lf = int(spark_str_lf.position)
  steerMsg.lb = int(spark_str_lb.position)
  steerMsg.rf = int(spark_str_rf.position)
  steerMsg.rb = int(spark_str_rb.position)
  str_pub.publish(steerMsg)

def arm_feedback():
    Pos_msg = ArmData()
    Vel_msg = ArmData()

    Pos_msg.ShoulderRot = spark_shoulderRot.position
    Pos_msg.ShoulderPitch = spark_shoulderPitch.position
    Pos_msg.ElbowPitch = spark_elbowPitch.position
    Pos_msg.WristPitch = spark_wristPitch.position
    Pos_msg.WristRot = spark_wristRot.position

    Vel_msg.ShoulderRot = spark_shoulderRot.velocity
    Vel_msg.ShoulderPitch = spark_shoulderPitch.velocity
    Vel_msg.ElbowPitch = spark_elbowPitch.velocity
    Vel_msg.WristPitch = spark_wristPitch.velocity
    Vel_msg.WristRot = spark_wristRot.velocity

    Pos_pub.publish(Pos_msg)
    Vel_pub.publish(Vel_msg)
  

'''
### CALLBACK FUNCTIONS ###
Each callback function is run whenever a topic changes it's value.
When the value changes, each callback function updates its relevant axis output.
Then as a safety measure, makes sure the percent out is between the values -100 and 100.
'''
def strCallback(data):
  global slf, slb, srf, srb
  slf = data.strLf
  if (slf > 100):
    slf = 100
  if (slf < -100):
    slf = -100

  slb = data.strLb
  if (slb > 100):
    slb = 100
  if (slb < -100):
    slb = -100

  srf = data.strRf
  if (srf > 100):
    srf = 100
  if (srf < -100):
    srf = -100

  srb = data.strRb
  if (srb > 100):
    srb = 100
  if (srb < -100):
    srb = -100


def driveCallback(data):
	global lf, lm, lb, rf, rm, rb
	lf = data.lf
	lm = data.lm
	lb = data.lb
	rf = data.rf
	rm = data.rm
	rb = data.rb
	print(lf, lm, lb, rf, rm, rb)

	if (lf > 100):
		lf = 100
	if (lf < -100):
		lf = -100

	if (lm > 100):
		lm = 100
	if (lm < -100):
		lm = -100

	if (lb > 100):
		lb = 100
	if (lb < -100):
		lb = -100

	if (rf > 100):
		rf = 100
	if (rf < -100):
		rf = -100

	if (rm > 100):
		rm = 100
	if (rm < -100):
		rm = -100

	if (rb > 100):
		rb = 100
	if (rb < -100):
		rb = -100

def driveSens_cb(data):
    global c_Scale
    temp = data.data
    if temp > 1.0:
      temp = 1.0
    if temp < 0:
      temp = 0
    c_Scale = c_Scale_Max*temp

def SR_cb(data):
    global ShoulderRot
    ShoulderRot = data.data
    if ShoulderRot > 100:
        ShoulderRot = 100
    if ShoulderRot < -100:
        ShoulderRot = -100

def SP_cb(data):
    global ShoulderPitch
    ShoulderPitch = data.data
    if ShoulderPitch > 100:
        ShoulderPitch = 100
    if ShoulderPitch < -100:
        ShoulderPitch = -100

def EP_cb(data):
    global ElbowPitch
    ElbowPitch = data.data
    if ElbowPitch > 100:
        ElbowPitch = 100
    if ElbowPitch < -100:
        ElbowPitch = -100

def WP_cb(data):
    global WristPitch
    WristPitch = data.data
    if WristPitch > 100:
        WristPitch = 100
    if WristPitch < -100:
        WristPitch = -100

def WR_cb(data):
    global WristRot
    WristRot = data.data
    if WristRot > 100:
        WristRot = 100
    if WristRot < -100:
        WristRot = -100

def armSens_cb(data):
    global c_ShoulderRot, c_ShoulderPitch, c_ElbowPitch, c_WristPitch, c_WristRot
    c_ShoulderRot = data.ShoulderRot
    c_ShoulderPitch = data.ShoulderPitch
    c_ElbowPitch = data.ElbowPitch
    c_WristPitch = data.WristPitch
    c_WristRot = data.WristRot
    if c_ShoulderRot > 1:
        c_ShoulderRot = 1
    elif c_ShoulderRot < 0:
        c_ShoulderRot = 0

    if c_ShoulderPitch > 1:
        c_ShoulderPitch = 1
    elif c_ShoulderPitch < 0:
        c_ShoulderPitch = 0

    if c_ElbowPitch > 1:
        c_ElbowPitch = 1
    elif c_ElbowPitch < 0:
        c_ElbowPitch = 0

    if c_WristPitch > 1:
        c_WristPitch = 1
    elif c_WristPitch < 0:
        c_WristPitch = 0

    if c_WristRot > 1:
        c_WristRot = 1
    elif c_WristRot < 0:
        c_WristRot = 0

def Drill_cb(data):
    global Drill
    Drill = data.data
    if Drill > 100:
        Drill = 100
    elif Drill < -100:
        Drill = -100

def DrillActuator_cb(data):
    global DrillActuator
    DrillActuator = data.data
    if DrillActuator > 100:
        DrillActuator = 100
    elif DrillActuator < -100:
        DrillActuator = -100

def setOutputs(lf, lm, lb, rf, rm, rb, str_lf, str_lb, str_rf, str_rb):
	spark_lf.velocity_output(lf * c_Scale * c_lfDir)
	spark_lm.velocity_output(lm * c_Scale * c_lmDir)
	spark_lb.velocity_output(lb * c_Scale * c_lbDir)
	spark_rf.velocity_output(rf * c_Scale * c_rfDir)
	spark_rm.velocity_output(rm * c_Scale * c_rmDir)
	spark_rb.velocity_output(rb * c_Scale * c_rbDir)

	spark_str_lf.position_output(str_lf * c_str_lfDir * c_str_Scale)
	spark_str_lb.position_output(str_lb * c_str_lbDir * c_str_Scale)
	spark_str_rf.position_output(str_rf * c_str_rfDir * c_str_Scale)
	spark_str_rb.position_output(str_rb * c_str_rbDir * c_str_Scale)

'''
### SNAPPING FUNCTION ###
This function is used in science system to "snap" the swab holder's position 
whenever it gets close to some specified swab positions.
'''   
def snap_function(publisher,input):
    snap_points = [9.405, 4.214, -1.07, -5.714, -10.214, -15, -19.19, -23.618]
    if input == 0:
        closest = min(snap_points, key=lambda x:abs(x-publisher.position))
        if abs(publisher.position - closest) < 3:
            publisher.position_output(closest)
        else:
            publisher.percent_output(input)
    else:
        publisher.percent_output(input)

def talker():
    global str_pub, lf, lm, lb, rf, rm, rb, c_Scale, c_str_Scale
    global c_lfDir, c_lmDir, c_lbDir, c_rfDir, c_rmDir, c_rbDir
    global ShoulderRot, ShoulderPitch, ElbowPitch, WristPitch, WristRot
    global Pos_pub, Vel_pub
    global snapping, snap_points, snap_status
    rospy.init_node("CAN_DTS")
    if rospy.get_param('~Snapping', 0.0) > 0:
        snapping = True
    else:
        snapping = False

    # Subscribers for drivetrain
    sub = rospy.Subscriber("Drive_Train", Drivetrain, driveCallback, queue_size = 10)
    str_sub = rospy.Subscriber("Steer_Train", Steertrain, strCallback, queue_size = 10)
    drive_sens = rospy.Subscriber("Drive/Drive_Sensitivity", Float64, driveSens_cb, queue_size=10)
    str_pub = rospy.Publisher("Drive/Steer_Feedback", Steer, queue_size=10)

    # Subscribers for Armtrain
    SR_sub = rospy.Subscriber("Arm/ShoulderRot", Float64, SR_cb, queue_size=10)
    SP_sub = rospy.Subscriber("Arm/ShoulderPitch", Float64, SP_cb, queue_size=10)
    EP_sub = rospy.Subscriber("Arm/ElbowPitch", Float64, EP_cb, queue_size=10)
    WP_sub = rospy.Subscriber("Arm/WristPitch", Float64, WP_cb, queue_size=10)
    WR_sub = rospy.Subscriber("Arm/WristRot", Float64, WR_cb, queue_size=10)
    arm_sens = rospy.Subscriber("Arm/Arm_Sensitivity", ArmData, armSens_cb, queue_size=10)
    Pos_pub = rospy.Publisher("Arm/JointPosition", ArmData, queue_size=10)
    Vel_pub = rospy.Publisher("Arm/JointVelocity", ArmData, queue_size=10)

    # Subscribers for Drill and Drill actuator for science.
    Drill_sub = rospy.Subscriber("Science/Drill", Float64, Drill_cb, queue_size=10)
    DrillActuator_sub = rospy.Subscriber("Science/DrillActuator", Float64, DrillActuator_cb, queue_size=10)

    setOutputs(0, 0, 0, 0, 0, 0, 0, 0, 0, 0)

    rosRate = rospy.Rate(30)    # hz

    while not rospy.is_shutdown():
        setOutputs(lf, lm, lb, rf, rm, rb, slf, slb, srf, srb)
        strpub()
        spark_shoulderRot.percent_output(c_ShoulderRot * ShoulderRot * c_ShoulderRotDir/100)
        spark_shoulderPitch.percent_output(c_ShoulderPitch * ShoulderPitch * c_ShoulderPitchDir/100)
        spark_elbowPitch.percent_output(c_ElbowPitch * ElbowPitch * c_ElbowPitchDir/100)
        spark_wristPitch.percent_output(c_WristPitch * WristPitch * c_WristPitchDir/100)
        if snapping:
            snap_function(spark_wristRot, c_WristRot * WristRot * c_WristRotDir/100)
        else:
            spark_wristRot.percent_output(c_WristRot * WristRot * c_WristRotDir/100)
        spark_Drill.percent_output(c_Drill * Drill * c_DrillDir/100)
        spark_DrillActuator.percent_output(c_DrillActuator * DrillActuator * c_DrillActuator/100)
        
        arm_feedback()
        rosRate.sleep()

if __name__ == '__main__':
    try:
        talker()
    except rospy.ROSInterruptException:
        pass

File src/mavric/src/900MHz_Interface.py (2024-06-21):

#!/usr/bin/env python
import rospy
import time
import os
from std_msgs.msg import Int32, String
from pySerialTransfer import pySerialTransfer as txfer
import driveMath


from mavric.msg import Drivetrain
from mavric.msg import Steertrain

port = '/dev/ttyACM1'

# Defaults and beginning values
drive = 0.0
steer = 0.0
mode = 0
parameters = [0,0,0,0,0,0,0,0,0,0]
deadzone = 0.05
sensitivity = 0.5
LoRaEnabled = False

class struct(object):
    drive = float
    steer = float
    mode = float


# Client Callback function that will run whenever the value for clients connected changes. 
# if connected clients is greater than zero, publish all zeros once and stop publishing to 
# stop interrupting websocket clients.
def client_cb(data):
    global LoRaEnabled
    val = int(data.data)
    if val == 0:
        LoRaEnabled = True
    else:
        if LoRaEnabled == True:
            drive.publish(0.0,0.0,0.0,0.0,0.0,0.0)
            steer.publish(0.0,0.0,0.0,0.0)
        LoRaEnabled = False


if __name__=='__main__':
    try:
        # Publishers and Subscribers
        drive = rospy.Publisher("/Drive/Drive_Command", Drivetrain, queue_size=10)
        steer = rospy.Publisher("/Drive/Steer_Command", Steertrain, queue_size=10)
        clients = rospy.Subscriber("client_count", Int32, client_cb, queue_size=10)
        rospy.init_node("LoRa_Radio")

        dataRX = struct
        link = txfer.SerialTransfer(port)   # setup serial transfer on port specified
        link.open() # open link between rover and LoRa

        while not rospy.is_shutdown():
            if link.available():    # Recieve new data from serial
                recSize = 0

                dataRX.drive = link.rx_obj(obj_type='f', start_pos=recSize)
                recSize += txfer.STRUCT_FORMAT_LENGTHS['f']

                dataRX.steer = link.rx_obj(obj_type='f', start_pos=recSize)
                recSize += txfer.STRUCT_FORMAT_LENGTHS['f']

                dataRX.mode = link.rx_obj(obj_type='f', start_pos=recSize)
                recSize += txfer.STRUCT_FORMAT_LENGTHS['f']

                if LoRaEnabled:
                    # Round data and test against deadzone
                    dataRX.drive = 100*round(dataRX.drive, 2)
                    dataRX.steer = 100*round(dataRX.steer, 2)
                    if abs(dataRX.drive) < deadzone:
                        dataRX.drive = 0
                    if abs(dataRX.steer) < deadzone:
                        dataRX.steer = 0

                    # Drive Modes given mode switch's setting
                    # Had to use floats to compare since the mode can't be transfered in an int.
                    if dataRX.mode < 0.5:
                        parameters = driveMath.car_drive(dataRX.drive*sensitivity,dataRX.steer)
                    elif dataRX.mode > 0.5:
                        parameters = driveMath.point_drive(dataRX.drive,dataRX.steer*sensitivity)

                    drive.publish(float(parameters[0]), float(parameters[1]), float(parameters[2]), float(parameters[3]), float(parameters[4]), float(parameters[5]))
                    steer.publish(float(parameters[6]), float(parameters[7]), float(parameters[8]), float(parameters[9]))
            elif link.status < 0:   # Error codes for Serial Transfer Library 
                print("No Message Recieved")
                if link.status == txfer.CRC_ERROR:
                    print('ERROR: CRC_ERROR')
                elif link.status == txfer.PAYLOAD_ERROR:
                    print('ERROR: PAYLOAD_ERROR')
                elif link.status == txfer.STOP_BYTE_ERROR:
                    print('ERROR: STOP_BYTE_ERROR')
                else:
                    print('ERROR: {}'.format(link.status))
                drive.publish(0,0,0,0,0,0)
                steer.publish(0,0,0,0)
    except rospy.ROSInterruptException:
        link.close()    # Close serial connection
        pass

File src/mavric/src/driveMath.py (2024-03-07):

#!/usr/bin/env python
import math


# Drive Math
# Jackson Milburn
# 2/19/2024


# The purpose of this script is to take in values from -100 to 100 for both the speed and direction from the controller.
# Using the dimensions of the wheelbase and track of the rover the script will return speed values from -100 to 100 representing the motor speeds of each wheel.
# The output of the direction of each wheel will be in degrees.
# The equations used to calculate both the speeds and directions were found from: https://www.mathworks.com/help/sm/ug/mars_rover.html


wheelbase = 42 # Wheelbase of the rover in inches
track = 26.5 # Track of the rover in inches
wheel_r = 5 # Radius of the wheel in inches

max_steer_angle = 45 # Max overall steering angle of the rover


# Initialzing speed and direction var for each wheel

FL_v = 0 # Front left angular velocity
FR_v = 0 # Front right angular velocity
ML_v = 0 # Mid left angular velocity
MR_v = 0 # Mid right angular velocity
BL_v = 0 # Back left angular velocity
BR_v = 0 # Back right angular velocity

FL_a = 0 # Front left angle
FR_a = 0 # Front right angle
BL_a = 0 # Back left angle
BR_a = 0 # Back right angle


def car_drive(drive, steer):

    # Checks for whether or not input from controller is within the 5% deadzone.

    if steer >= -5 and steer <= 5:

        # Initializing velocity and steering vars

        steer_angle = 0
        FR_a = 0
        FL_a = 0
        FL_v = drive
        FR_v = drive
        ML_v = drive
        MR_v = drive

    else:

        steer_angle = steer*math.radians(max_steer_angle)*0.01 # Converts -100 to 100 value into angle in radians
        R = (wheelbase/2)/math.tan(steer_angle) # Calculates the turn radius

        FR_a = math.degrees(math.atan((wheelbase/2)/(R-track/2))) # Calculates front right angle in degrees
        FL_a = math.degrees(math.atan((wheelbase/2)/(R+track/2))) # Calculates front left angle in degrees

        FL_v = (drive*math.sqrt((wheelbase/2)**2+(R+track/2)**2))/R # Calculates front left velocity from -100 to 100
        FR_v = (drive*math.sqrt((wheelbase/2)**2+(R-track/2)**2))/R # Calculates front right velocity from -100 to 100


        # Checks for proper sign for angles

        if steer < 0: 
            FL_v = -FL_v
            FR_v = -FR_v


        # Checks for proper velocity adjustment depenting on turn direction
            
        if abs(FL_v) > abs(FR_v) and abs(FL_v) > 100:
            v_adj = abs(FL_v*0.01)
        elif abs(FR_v) > abs(FL_v) and abs(FR_v) > 100:
            v_adj = abs(FR_v*0.01)
        else:
            v_adj = 1


        # Calculates the velocity of each wheel depending on the velocity adjustment and turn direction

        FL_v = FL_v/v_adj
        FR_v = FR_v/v_adj
        ML_v = (drive*(R+track/2))/R/v_adj
        MR_v = (drive*(R-track/2))/R/v_adj

    # Assigning correct magnitude and sign to the opposing wheel velocity and angle

    BL_a = -FL_a
    BR_a = -FR_a

    BL_v = FL_v
    BR_v = FR_v

    return [FL_v, ML_v, BL_v, FR_v, MR_v, BR_v, FL_a, BL_a, FR_a, BR_a]


def point_drive(drive,steer):

    outer_pd_R = math.sqrt((track/2)**2 + (wheelbase/2)**2) # Radius of the outer wheels
    inner_pd_R = track/2 # Radius of the inner wheels (middle)

    pd_angle = math.degrees(math.atan(outer_pd_R/inner_pd_R)) # Angle of the outer wheels in point drive

    v_adj = inner_pd_R/outer_pd_R # Ratio of the inner to outer radius


    # Adjusts the velocity and direction of each respective wheel

    FL_v = steer
    ML_v = steer*v_adj
    BL_v = steer
    FR_v = -steer
    MR_v = -steer*v_adj
    BR_v = -steer


    # Adjusts the correct direction of the outer wheel angles

    FL_a = pd_angle
    BL_a = -pd_angle
    FR_a = -pd_angle
    BR_a = pd_angle

    return [FL_v, ML_v, BL_v, FR_v, MR_v, BR_v, FL_a, BL_a, FR_a, BR_a]

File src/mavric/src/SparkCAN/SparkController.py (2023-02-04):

from can.interface import Bus
from can import Message
from Statuses import Status
from struct import pack

"""
Description: Objects for storing data from motor controllers and sending data to motor controllers
Author: Jacob Peskuski, Gabriel Carlson
"""


def packer_float(value):
    hexStr = pack('fi', value, 0)
    return hexStr


class Controller:
    def __init__(self, bus, id):
        self.bus = bus
        self.id = id
        self.statuses = {0x60: None,
                         0x61: Status(0x2051840+id, (32, 8, 12, 12), ('float', 'uint', 'uint', 'uint')),
                         0x62: Status(0x2051880+id, (32,), ('float',)),
                         0x63: None,
                         0x64: None}

        # control properties
        self.percentProps = {"dir": 1, "scale": 1}
        self.velocityProps = {"dir": 1, "countConversion": 1}
        self.positionProps = {"dir": 1, "countConversion": 1}

    def enable(self):
        pass
        # TODO: Send enable control message to motor controller

    def disable(self):
        pass
        # TODO: Send disable control message to motor controller

    def percent_output(self, value):
        mod_value = value*self.percentProps["dir"]*self.percentProps["scale"]
        msg = Message(arbitration_id= 0x02050080 + self.id, data=packer_float(mod_value))
        self.bus.send_msg(msg)

    def velocity_output(self, value):
        mod_value = value * self.velocityProps["dir"]*self.velocityProps["countConversion"]
        msg = Message(arbitration_id= 0x02050480 + self.id, data=packer_float(mod_value))
        self.bus.send_msg(msg)

    def position_output(self, value):
        mod_value = value * self.positionProps["dir"]*self.positionProps["countConversion"]
        msg = Message(arbitration_id= 0x02050C80 + self.id, data=packer_float(mod_value))
        self.bus.send_msg(msg)

    @property
    def velocity(self):
        return self.statuses[0x61].data[0]

    @property
    def position(self):
        return self.statuses[0x62].data[0]

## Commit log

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2017-06-14 Added Pi Zero HAT Template
    The template has backpowering protection and the required EEPROM for HAT
    identification
    [HAT.kicad_pcb, HAT.sch, PowerProtection.sch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]
2017-06-14 Shrunk HAT template resistors
    [HAT.kicad_pcb, HAT.sch, PowerProtection.sch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]
2017-06-15 Added I2C pullups to the HAT template for the device bus
    Most boards (if not all) will use I2C for communication on the board.
    [HAT.kicad_pcb, HAT.sch, PowerProtection.sch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]
2017-07-13 Added preliminary power budget spreadsheet
    [PowerBudget.xlsm]
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2017-08-04 Moved electrical documents over
    [HAT.kicad_pcb, HAT.sch, PowerBudget.xlsm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]
2017-08-07 Updated the power budget and added a tab-separated export
    [PowerBudget.xlsm]
2017-08-08 Made a new power budget with current calculations. Allows for an arbitrary tree/forest structure.
    [PowerBudget.xlsm, PowerBudget.xlsx]
2017-08-08 I thought I removed the old earlier.
    [PowerBudget.xlsm]
2017-08-08 Changed all refereces to structured (table) refrences, including column values in VLOOKUPs.
    [PowerBudget.xlsx]
2017-08-08 Updates to the Power Budget workbook
    [PowerBudget.xlsx]
2017-08-08 Added a sample of using a higher-voltage battery with a regulator
    [PowerBudget.xlsx]
2017-08-08 Added the RM3 and antenna, also blanked out unfilled rows in analysis and results
    [PowerBudget.xlsx]
2017-08-08 Adjusted motor currents to something closer to reality (not always at stall) and changed results color coding
    [PowerBudget.xlsx]
2017-08-08 Added Power Rail Summary
    [PowerBudget.xlsx]
2017-08-08 Added a Costs summary and differentiation of peak and constant current/power. Battery life is based on constant consumption.
    [PowerBudget.xlsx]
2017-08-08 Added an items table back in, it allows the user to configure overrides. An exmple is provided with a tunable linear regulator component. One is configures as the 12V supply, the other as the 5V supp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
    [PowerBudget.xlsx]
2017-08-09 Added an efficiency parameter, the self consumption is increased by it's passed-on power*(1-efficiency)
    [PowerBudget.xlsx]
2017-08-11 Changed efficiency to Transmission Loss
    [PowerBudget.xlsx]
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2017-09-30 Added BLDC controllers to the power budget.
    Brushless DC motors are lighter, and give better performance (with
    cheaper ESC's it looks like)
    [PowerBudget.xlsx]
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2017-11-27 Added the HAT design to the project
    [Drive Board Connector HAT.fzz]
2017-11-27 Updated the location of a part label
    [Drive Board Connector HAT.fzz]
2017-11-28 Fixed some schematic stuff
    [Drive Board Connector HAT.fzz]
2017-11-28 Improved the routing a bit.
    [Drive Board Connector HAT.fzz]
2018-01-18 Add files via upload
    List of designs for the command strings that will be sent to the rover. Comments/Improvements are welcomed?
    [Command Strings List.xlsx]
2018-01-22 Added Arm power supplies to the power budget.
    [PowerBudget.xlsx]
2018-01-22 Corrected battery life units.
    [PowerBudget.xlsx]
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2018-03-03 Fixed the PWM output period to match the specs for the ESCs
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2018-03-14 Updates to the electrical design documents
    [PowerBudget.xlsx]
2018-03-19 Added the option to set output voltage equal to input voltage.
    [PowerBudget.xlsx]
2018-03-19 Added battery discharge rate
    [PowerBudget.xlsx]
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2018-03-22 Removed global channel variables, the drive-train will now support hot-swapping PWM assignments.
2018-03-28 Updates to power budget and diagrams
    [PowerBudget.xlsx]
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2018-04-03 Updates to the power budget.
    1. Removed the arm.
    2. Moved [INPUT] substitution to the items page
    3. Updated the costs page.
    [PowerBudget.xlsx]
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2018-06-21 Updatd the command strings file to reflect changes to the drivertain.
    [Command Strings List.xlsx]
2018-07-21 Modified the power budget.
    [PowerBudget.xlsx]
2018-07-21 Fixed the repo on the Drive board
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2018-07-26 Successful GPS module interface. I still haven't checked it getting a good fix, but it turns out that it works fine, if you press the power key on startup. We can add a relay or something to do that 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
2018-07-27 Added E-Box changes to the power budget
    [PowerBudget.xlsx]
2018-07-27 Updated the command strings to include GPS endpoint
    [Command Strings List.xlsx]
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2018-07-28 Updated the command strings to match development progress
    [Command Strings List.xlsx]
2018-07-29 Fixed an issue in the Drive_Train_S.py (uneeded import) and added a 'simulated' argument to the launch files that allows the system to launch on a non-MAVRIC machine by disabling nodes that require s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
2018-08-01 Update to power budget
    [PowerBudget.xlsx]
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2018-08-05 Minor changes to power budget document
    [PowerBudget.xlsx]
2018-08-06 Updated the command strings list
    The arm is not currently consistent with the code, but that's because
    the code is unfinished.
    [Command Strings List.xlsx]
2018-08-12 Minor changes to the power budget
    [PowerBudget.xlsx]
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2018-10-13 Added ramping to some of the arm nodes (the ones most succeptable to oscillation)
    [Ramping.py]
2018-10-13 Update autonomous message formats
    Updated autonomous command strings. Added message types for controlling
    the autonomous system.
    [Command Strings List.xlsx]
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2018-10-27 Added radius turning, added waypoint clearing
    Added functions to allow radius turning instead of point turning. Added
    a command to erase all waypoints (useful for testing). Removed some
    debug prints.
    [Command Strings List.xlsx]
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2018-12-07 Added preliminary Power distro board
    $27.6 board (2.3"x2.4" 2-layer) with 1->5 each split for 2 busses
    (intended for 22V and 12V)
    [Arm Power Distribution.kicad_pcb, Arm Power Distribution.sch]
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2018-12-09 Added an 8-channel ADC HAT (10 kHz chip)
    [Arm Power Distribution.kicad_pcb, HAT.kicad_pcb, HAT.sch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]
2018-12-10 Re-routed the ADC board (package type mistake)
    [HAT.kicad_pcb, HAT.sch]
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2019-02-09 Correct missing ground on C1,C2
    [HAT-B.Cu.gbr, HAT-B.Mask.gbr, HAT-B.SilkS.gbr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]
2019-02-09 Fix silkscreen
    [HAT.kicad_pcb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]
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2019-10-12 Quick fix to arm shoulder rotation
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2020-04-17 Added Jetson interface board to Git
    Included the Jetson interface board KiCAD design in the repository for
    safekeeping.
    [DigiKey_BOM.xlsx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]
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2020-09-27 Added CAN tank drive, temporary fan control fixes for bad interface board
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2021-10-02 Fixed: Undefined mavric GPS msg bug
    [GPS_Streamer.py]
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2021-10-06 Fixed: Missing num satellites on gps publish
    [GPS_Streamer.py]
2021-10-06 Removed: Fix bool from GPS_data, added GPS_Fix
    [GPS_Streamer.py]
2021-10-07 Fixed: Timestamps on GPS Streamer
    [GPS_Streamer.py]
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2021-10-14 Fixed: Pin 16 not working, switched to 40
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2021-11-13 Fixed IMU offset
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2021-11-16 Troubleshooted autonomous and fixed gps interface.
    [BNO055_IMU.py]
2021-11-17 Fixed LED_Control.py
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2022-03-11 Troubleshooted PID test. Found some decent K constants and found some issues with encoder feedback.
    [LinearMapping.py]
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2023-02-21 fixed CMake file. Shoulder Pitch works now!
    [SparkCAN_Drive_Train.py]
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2023-02-27 reversed pitch controls
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2023-10-19 Revert "led test code with export env"
    This reverts commit 97c5f2826fa98399b3dd90a31399ce1427c1d2b8.
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2023-11-02 attempt 1 at fixing stuttering
    [900MHz_Interface.py]
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2023-11-15 reworked drive so only one script accesses can bus
    [SparkCAN_Drive_Train.py]
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2023-11-28 Delete src/mavric/src/RTSP_Camera.py
    File is no longer needed, as the camera runs from HTTP script.
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2024-02-13 Reworked drive math to output values for v and ang
    [driveMath.py]
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2024-02-16 some small fixes to gps geodesic calculation and more led debug
    [LED_Strip.py]
2024-02-16 test script for the new gps. Not working currently
    [GPS_Neo-M9N.py]
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2024-04-06 positon feedback fixed and swab position snapping now works!
    [SparkCAN_Drive_Train.py]
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2024-05-21 in person testing and fixes 5/21
    [PTZ_Control.py]
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
